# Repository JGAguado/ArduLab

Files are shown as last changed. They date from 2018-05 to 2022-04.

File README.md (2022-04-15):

[][releases]
[](LICENSE)

[][maintenance]
[][buymecoffee]

# ArduLab

The ArduLab board is a robotic platform designed for the ICAI Technological Campus. It has been created with educational purposes for developing robotic proyects based on de [Arduino](https://www.arduino.cc) environment.

<p float="left">
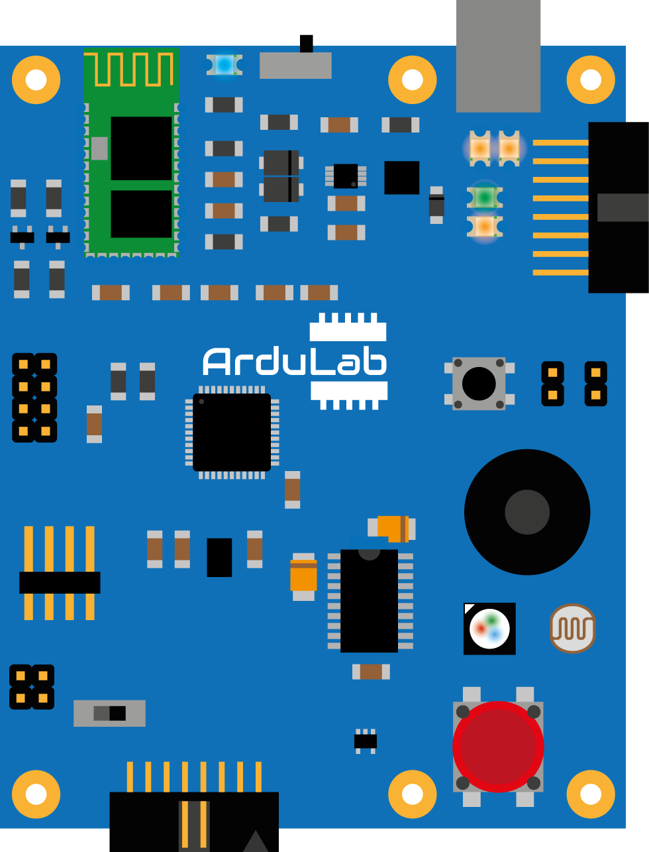
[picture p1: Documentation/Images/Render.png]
   
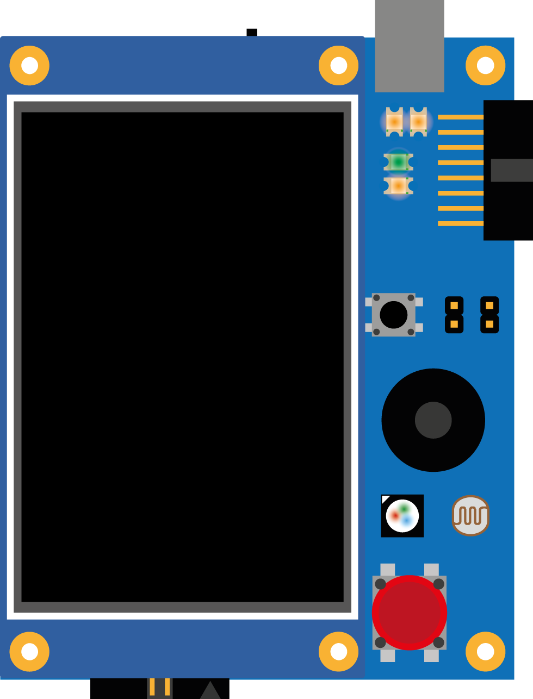
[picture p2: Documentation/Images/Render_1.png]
   
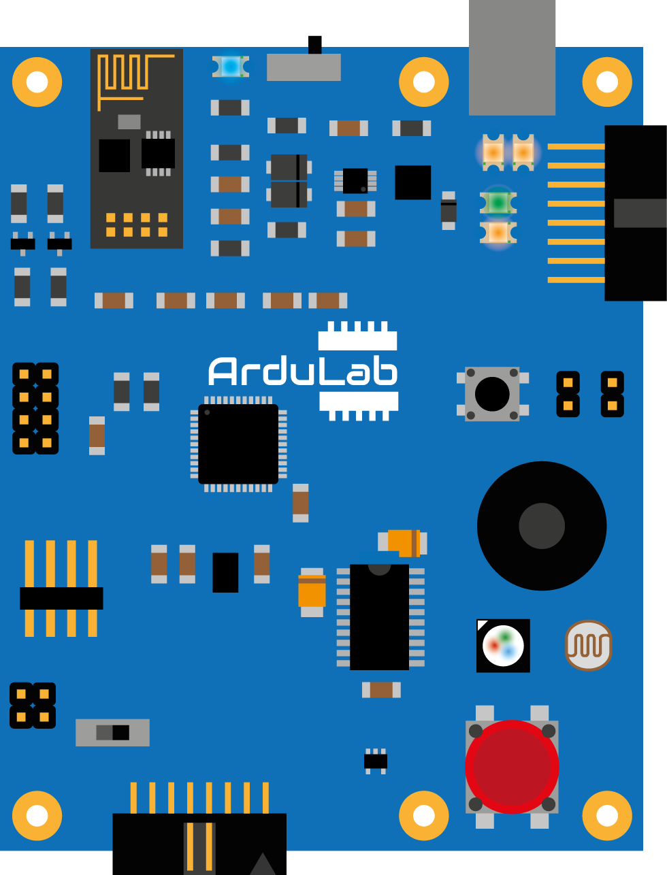
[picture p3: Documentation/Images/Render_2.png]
   
</p>

## Features
* Atmega32U4 microcontroller (same as Arduino Leonardo)
* RGB Led
* LDR
* Buzzer
* Pushbutton
* DC Motor driver (H-Bridge)
* LiPo charging system
* Bluetooth connectivity (HC-05)

It supports the [Itead Nextion Displays](https://www.itead.cc/display/nextion.html) via serial port and also can be plugged directly to the [ElectroLab](https://github.com/SpaceDIY/ElectroLab) board to expand it's functions!

## Project tree

<li><a href="./Hardware/">Hardware</a></li>
<li><a href="./Firmware/">Firmware</a></li>
<li><a href="./Documentation/">Documentation</a></li>

<li><a href="./README.md">README.md</a></li>

[releases-shield]: https://img.shields.io/github/release/JGAguado/ArduLab.svg?style=for-the-badge
[releases]: https://github.com/JGAguado/ArduLab/releases

[license-shield]: https://img.shields.io/badge/License-CC%20BY--NC--SA%204.0-lightgrey.svg?style=for-the-badge

[maintenance-shield]: https://img.shields.io/badge/maintainer-J.%20G.%20Aguado-blue.svg?style=for-the-badge
[maintenance]: https://github.com/JGAguado

[buymecoffee-shield]: https://img.shields.io/badge/buy%20me%20a%20coffee-support-yellow.svg?style=for-the-badge
[buymecoffee]: https://www.buymeacoffee.com/J.G.Aguado

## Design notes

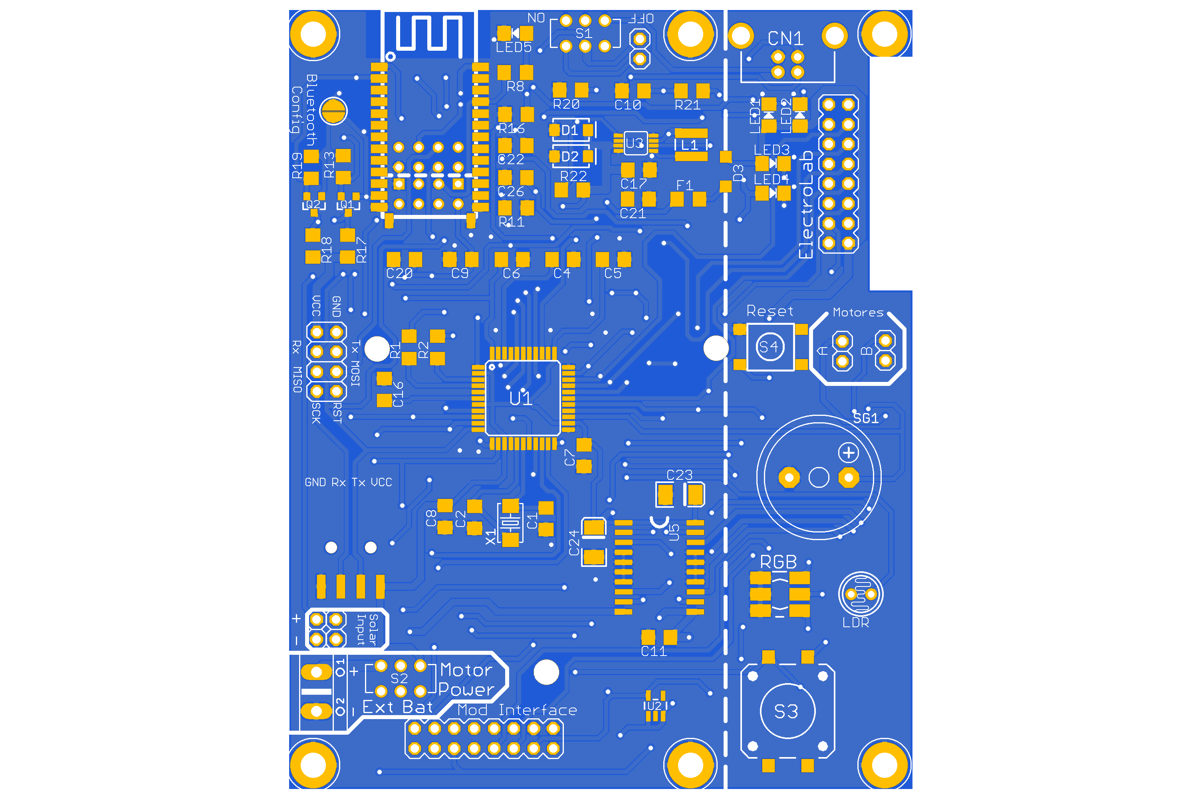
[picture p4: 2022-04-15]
Documentation/Images/Top.png

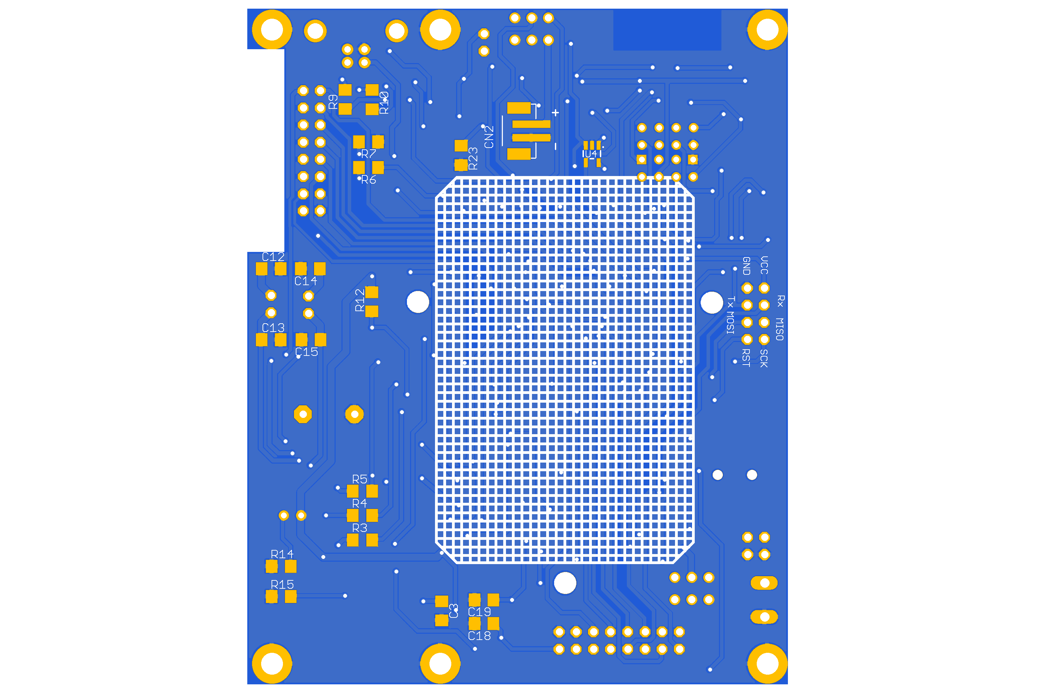
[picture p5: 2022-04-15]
Documentation/Images/Bottom.png

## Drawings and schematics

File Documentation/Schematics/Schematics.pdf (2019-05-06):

A

A

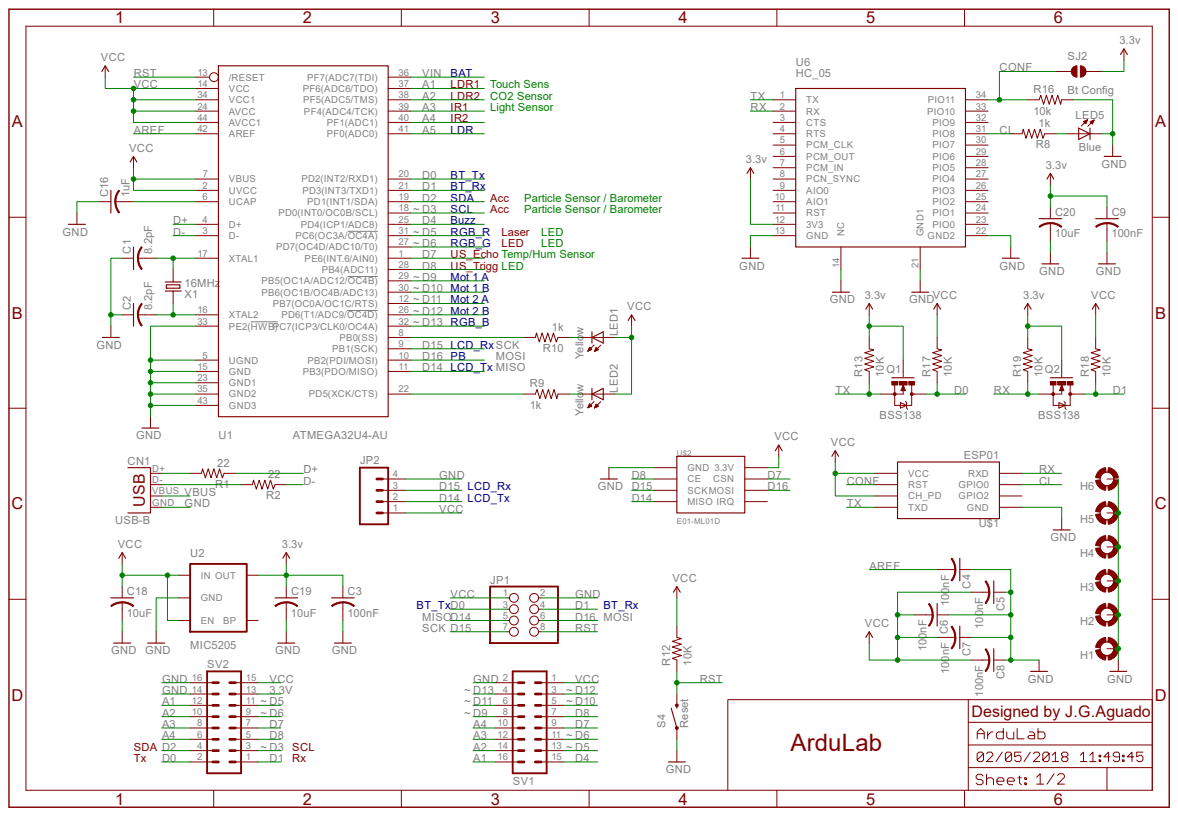
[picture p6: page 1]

A

A

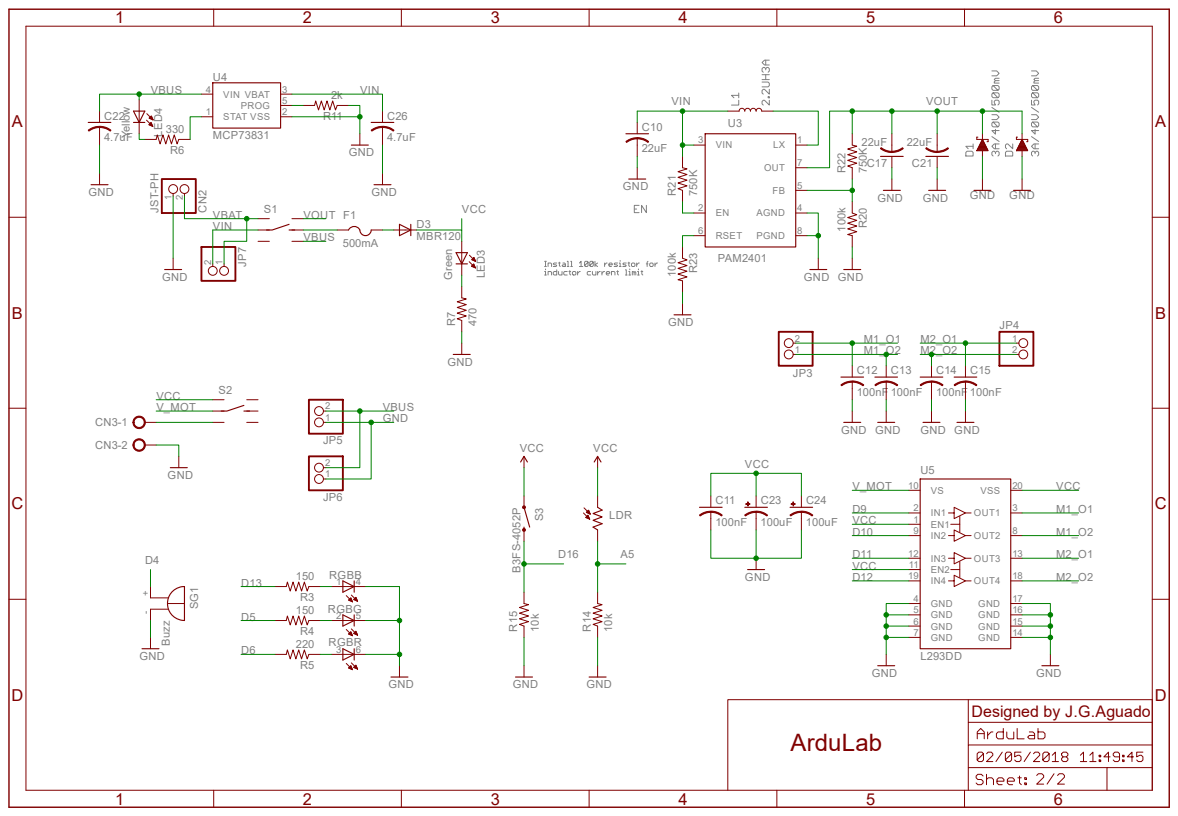
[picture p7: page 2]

GND 14 GND 15 GND 16 GND 17

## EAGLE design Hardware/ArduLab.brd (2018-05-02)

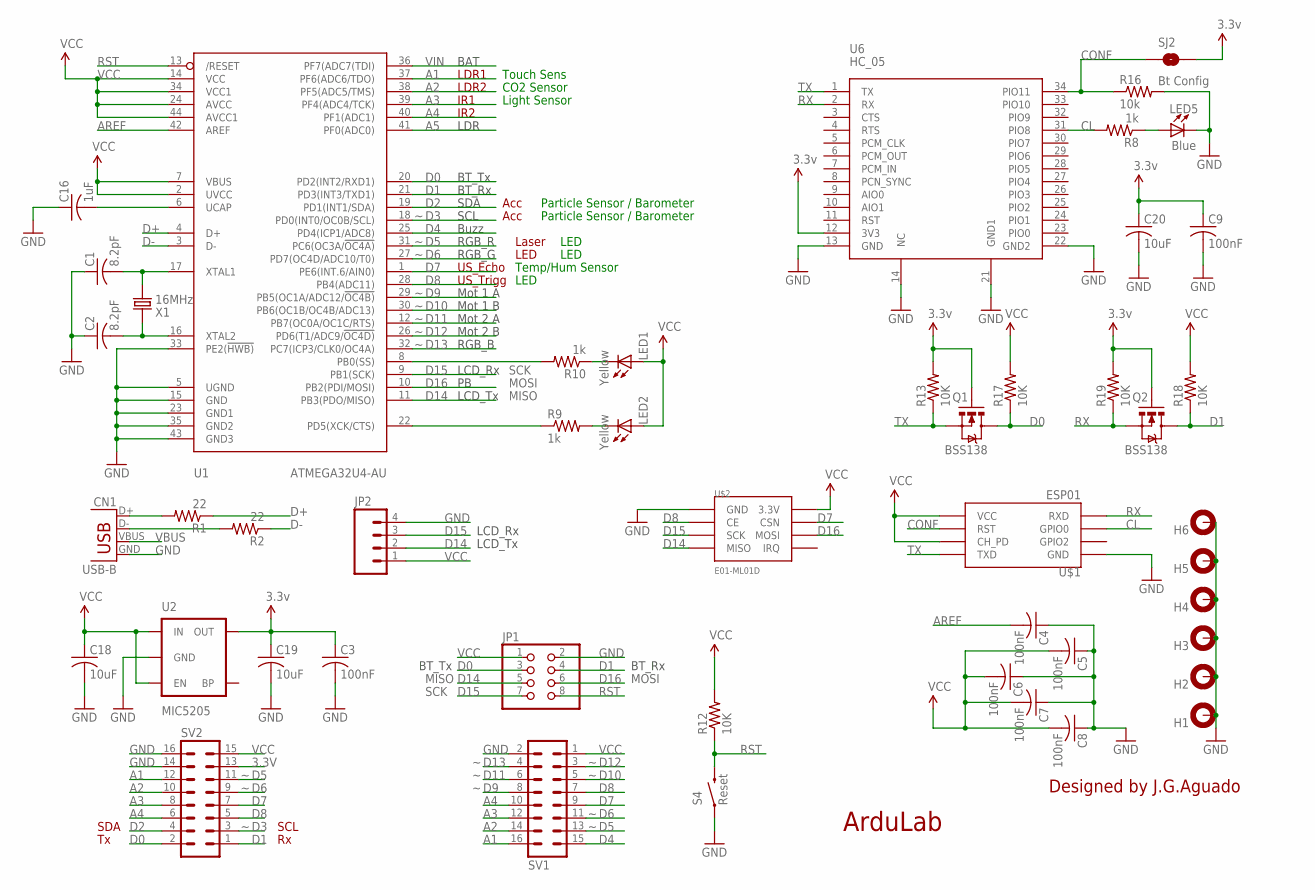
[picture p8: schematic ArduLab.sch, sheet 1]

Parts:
C1, C2: 8.2pF; C1206
C3, C4, C5, C6, C7, C8, C9: 100nF; C1206
C16: 1uF; C1206
C18, C19, C20: 10uF; C1206
CN1: USB-B; USB-B-PTH
H1, H2, H3, H4, H5, H6: MOUNT-PAD-ROUND3.2; 3,2-PAD
JP1: PINHD-2X4; 2X04
JP2: M04SMD; 1X04-SMD
LED1, LED2: Yellow; LED1206
LED5: Blue; LED1206
Q1, Q2: BSS138; SOT23-3
R1, R2: 22; R1206
R8, R9, R10: 1k; R1206
R12, R13, R17, R18, R19: 10K; R1206
R16: 10k; R1206
S4: Reset; TACTILE_SWITCH_TALL
SJ2: Bt Config; SJ_ROUND
SV1, SV2: MA08-2
U1: ATMEGA32U4-AU; TQFP44
U2: MIC5205; SOT23-5
U6: HC_05; BLUETOOTH_SMD
U$1: ESP01
U$2: E01-ML01D
X1: 16MHz; 2P-SMD-5X3.2

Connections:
3.3V: C3.1, C9.1, C19.1, C20.1, Q1.1 (G), Q2.1 (G), R13.2, R19.2, SJ2.2, SV2.13, U2.5 (OUT), U6.12 (3V3), U$1.CH_PD, U$1.VCC, U$2.P$2 (3.3V)
A1: SV1.16, SV2.12, U1.37 (PF6(ADC6/TDO))
A2: SV1.14, SV2.10, U1.38 (PF5(ADC5/TMS))
A3: SV1.12, SV2.8, U1.39 (PF4(ADC4/TCK))
A4: SV1.10, SV2.6, U1.40 (PF1(ADC1))
A5: U1.41 (PF0(ADC0)); also elsewhere on the board
AREF: C4.2, U1.42 (AREF)
CL: R8.2, U6.31 (PIO8), U$1.GPIO0
CONF: R16.1, SJ2.1, U6.34 (PIO11), U$1.RST
D0: JP1.3, Q1.3 (D), R17.1, SV2.2, U1.20 (PD2(INT2/RXD1))
D1: JP1.4, Q2.3 (D), R18.1, SV2.1, U1.21 (PD3(INT3/TXD1))
D2: SV2.4, U1.19 (PD1(INT1/SDA))
D3: SV2.3, U1.18 (PD0(INT0/OC0B/SCL))
D4: SV1.15, U1.25 (PD4(ICP1/ADC8)); also elsewhere on the board
D5: SV1.13, SV2.11, U1.31 (PC6(OC3A/!OC4A)); also elsewhere on the board
D6: SV1.11, SV2.9, U1.27 (PD7(OC4D/ADC10/T0)); also elsewhere on the board
D7: SV1.9, SV2.7, U1.1 (PE6(INT.6/AIN0)), U$2.P$4 (CSN)
D8: SV1.7, SV2.5, U1.28 (PB4(ADC11)), U$2.P$3 (CE)
D9: SV1.8, U1.29 (PB5(OC1A/ADC12/!OC4B)); also elsewhere on the board
D10: SV1.5, U1.30 (PB6(OC1B/OC4B/ADC13)); also elsewhere on the board
D11: SV1.6, U1.12 (PB7(OC0A/OC1C/RTS)); also elsewhere on the board
D12: SV1.3, U1.26 (PD6(T1/ADC9/!OC4D)); also elsewhere on the board
D13: SV1.4, U1.32 (PC7(ICP3/CLK0/OC4A)); also elsewhere on the board
D14: JP1.5, JP2.2, U1.11 (PB3(PDO/MISO)), U$2.P$7 (MISO)
D15: JP1.7, JP2.3, U1.9 (PB1(SCK)), U$2.P$5 (SCK)
D16: JP1.6, U1.10 (PB2(PDI/MOSI)), U$2.P$6 (MOSI); also elsewhere on the board
D17/PB0/RXLED: R10.2, U1.8 (PB0(SS))
D+: R1.1, U1.4 (D+)
D-: R2.1, U1.3 (D-)
GND: C1.1, C2.1, C3.2, C4.1, C5.1, C6.1, C7.1, C8.1, C9.2, C16.1, C18.2, C19.2, C20.2, CN1.GND, H1.B3,2, H2.B3,2, H3.B3,2, H4.B3,2, H5.B3,2, H6.B3,2, JP1.2, JP2.4, LED5.C, R16.2, S4.A2 (1), SV1.2, SV2.14, SV2.16, U1.5 (UGND), U1.15 (GND), U1.23 (GND1), U1.33 (PE2(!HWB)), U1.35 (GND2), U1.43 (GND3), U2.2 (GND), U6.13 (GND), U6.14 (NC), U6.21 (GND1), U6.22 (GND2), U$1.GND, U$2.P$1 (GND); also elsewhere on the board
unnamed: C1.2, U1.17 (XTAL1), X1.2
unnamed: C2.2, U1.16 (XTAL2), X1.1
unnamed: LED2.C, R9.2
unnamed: LED1.C, R10.1
unnamed: CN1.D+, R1.2
unnamed: CN1.D-, R2.2
unnamed: LED5.A, R8.1
PD5/TXLED: R9.1, U1.22 (PD5(XCK/CTS))
RST: JP1.8, R12.1, S4.B2 (2), U1.13 (/RESET)
RX: Q2.2 (S), R19.1, U6.2 (RX), U$1.RX (RXD)
TX: Q1.2 (S), R13.1, U6.1 (TX), U$1.TX (TXD)
UCAP: C16.2, U1.6 (UCAP)
VBUS: CN1.VBUS; also elsewhere on the board
VCC: C5.2, C6.2, C7.2, C8.2, C18.1, JP1.1, JP2.1, LED1.A, LED2.A, R12.2, R17.2, R18.2, SV1.1, SV2.15, U1.2 (UVCC), U1.7 (VBUS), U1.14 (VCC), U1.24 (AVCC), U1.34 (VCC1), U1.44 (AVCC1), U2.1 (IN), U2.3 (EN); also elsewhere on the board
VIN: U1.36 (PF7(ADC7(TDI)); also elsewhere on the board

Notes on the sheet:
ArduLab
Designed by J.G.Aguado
SCK
MOSI
MISO
BAT
BT_Tx
BT_Rx
Acc
Buzz
Mot 1 A
Mot 1 B
Mot 2 B
Mot 2 A
RGB_B
LCD_Tx
LCD_Rx
LDR1
LDR2
IR1
IR2
SDA
SCL
Laser
LED
US_Echo
US_Trigg
Touch Sens
CO2 Sensor
Light Sensor
Particle Sensor / Barometer
Temp/Hum Sensor
RGB_R
RGB_G
LDR

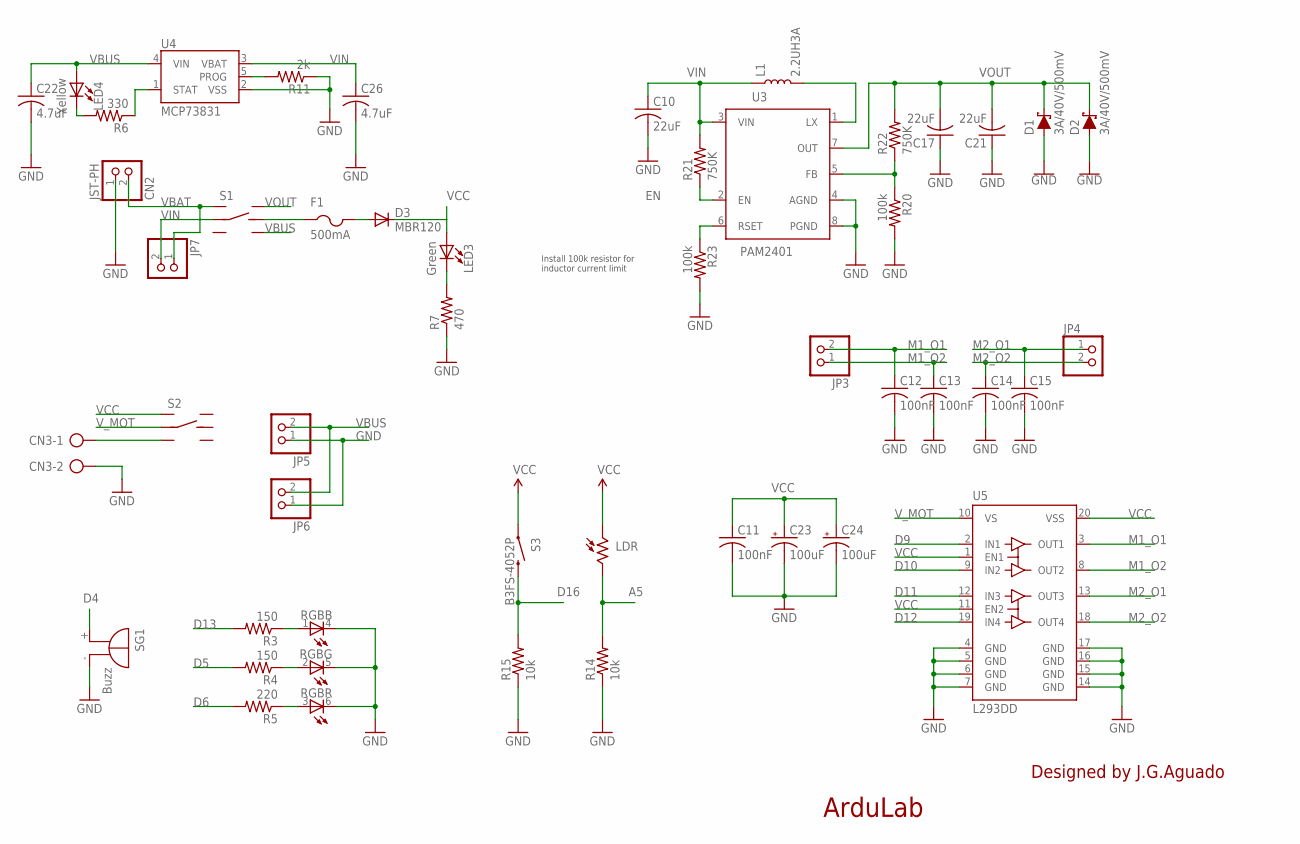
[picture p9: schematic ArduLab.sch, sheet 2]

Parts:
C10, C17, C21: 22uF; C1206
C11, C12, C13, C14, C15: 100nF; C1206
C22, C26: 4.7uF; C3216
C23, C24: 100uF; EIA3528-KIT
CN2: JST-PH; JST-PH-2-SMT
CN3: AK500/2
D1, D2: 3A/40V/500mV; SMA-DIODE
D3: MBR120; SOD123
F1: 500mA; R1206
JP3, JP4, JP5, JP6, JP7: PINHD-1X2; 1X02
L1: 2.2UH3A; INDUCTOR_4X4MM
LDR: VT20N1; TO46-VT200
LED3: Green; LED1206
LED4: Yellow; LED1206
R3, R4: 150; R1206
R5: 220; R1206
R6: 330; R1206
R7: 470; R1206
R11: 2k; R1206
R14, R15: 10k; R1206
R20, R23: 100k; R1206
R21, R22: 750K; R1206
RGB: OVSTRGBBCR8_V2
S1, S2: DPDT_JS202011CQN
S3: B3FS-4052P; TACTILE-SMD-12MM
SG1: Buzz; F/HMB
U3: PAM2401; MSOP8
U4: MCP73831; SOT23-5
U5: L293DD; SO20

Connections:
A5: LDR.2, R14.2; also elsewhere on the board
D4: SG1.+; also elsewhere on the board
D5: R4.2; also elsewhere on the board
D6: R5.2; also elsewhere on the board
D9: U5.2 (IN1); also elsewhere on the board
D10: U5.9 (IN2); also elsewhere on the board
D11: U5.12 (IN3); also elsewhere on the board
D12: U5.19 (IN4); also elsewhere on the board
D13: R3.2; also elsewhere on the board
D16: R15.2, S3.3 (2); also elsewhere on the board
EN: R21.1, U3.2 (EN)
GND: C10.2, C11.2, C12.2, C13.2, C14.2, C15.2, C17.1, C21.1, C22.2, C23.C (-), C24.C (-), C26.2, CN2.1 (2), CN3.2, D1.A, D2.A, JP5.1, JP6.1, R7.1, R11.1, R14.1, R15.1, R20.2, R23.2, RGB.4 (C), RGB.5 (C), RGB.6 (C), SG1.-, U3.4 (AGND), U3.8 (PGND), U4.2 (VSS), U5.4 (GND), U5.5 (GND), U5.6 (GND), U5.7 (GND), U5.14 (GND), U5.15 (GND), U5.16 (GND), U5.17 (GND); also elsewhere on the board
M1_O1: C12.1, JP3.2, U5.3 (OUT1)
M1_O2: C13.1, JP3.1, U5.8 (OUT2)
M2_O1: C15.1, JP4.1, U5.13 (OUT3)
M2_O2: C14.1, JP4.2, U5.18 (OUT4)
unnamed: R20.1, R22.1, U3.5 (FB)
unnamed: F1.1, S1.5 (RC)
unnamed: L1.P$2 (2), U3.1 (LX)
unnamed: R23.1, U3.6 (RSET)
unnamed: LED4.C, R6.2
unnamed: R11.2, U4.5 (PROG)
unnamed: R6.1, U4.1 (STAT)
unnamed: LED3.C, R7.2
unnamed: D3.A, F1.2
unnamed: R3.1, RGB.1 (A)
unnamed: R4.1, RGB.2 (A)
unnamed: R5.1, RGB.3 (A)
VBAT: CN2.2 (1), JP7.1, S1.1 (L1)
VBUS: C22.1, JP5.2, JP6.2, LED4.A, S1.6 (R2), U4.4 (VIN); also elsewhere on the board
VCC: C11.1, C23.A (+), C24.A (+), D3.C, LDR.1, LED3.A, S2.1 (L1), S3.1, U5.1 (EN1), U5.11 (EN2), U5.20 (VSS); also elsewhere on the board
VIN: C10.1, C26.1, JP7.2, L1.P$1 (1), R21.2, S1.2 (LC), U3.3 (VIN), U4.3 (VBAT); also elsewhere on the board
VOUT: C17.2, C21.2, D1.C, D2.C, R22.2, S1.4 (R1), U3.7 (OUT)
V_AUX: CN3.1, S2.3 (L2)
V_MOT: S2.2 (LC), U5.10 (VS)

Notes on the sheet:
ArduLab
Designed by J.G.Aguado
Install 100k resistor for inductor current limit

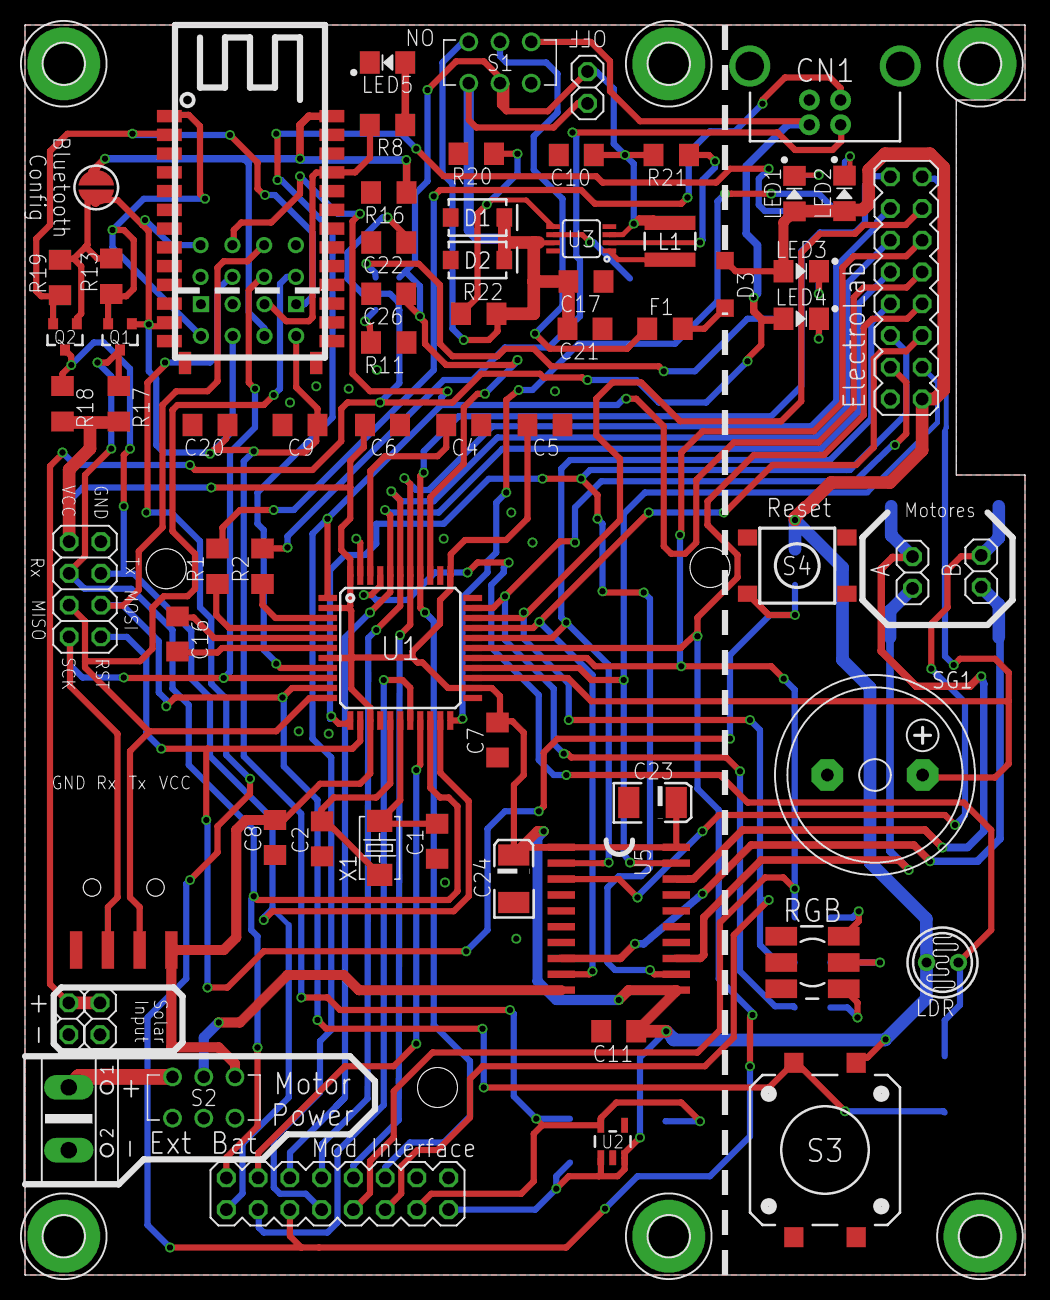
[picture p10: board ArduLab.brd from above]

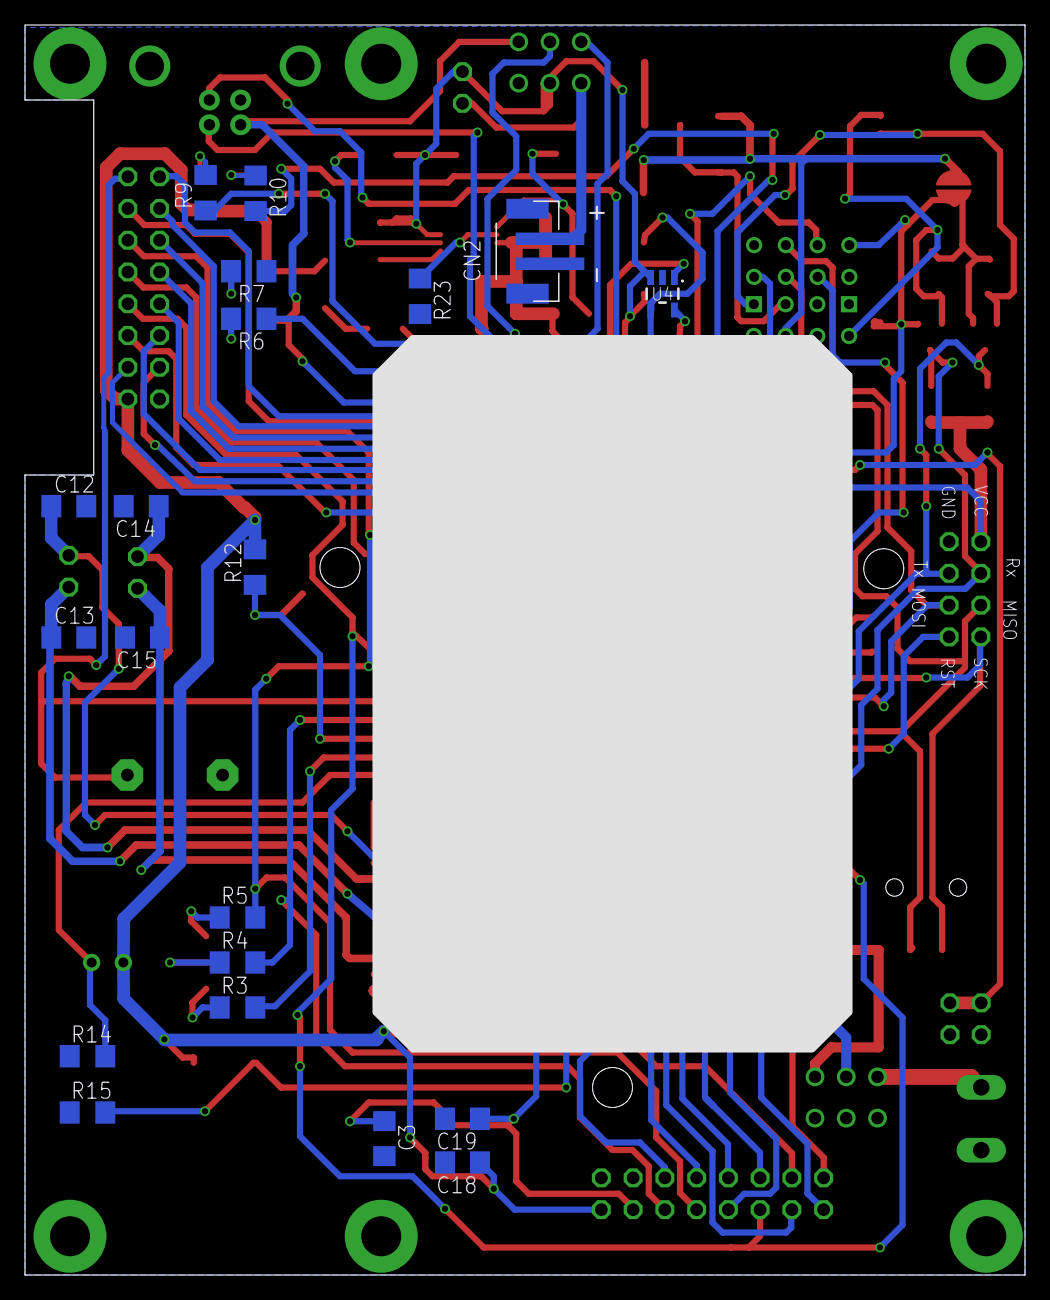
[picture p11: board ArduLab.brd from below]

Board: 2 copper layers, 80.0 x 100.0 mm, 95 parts (20 on the bottom side), 66 nets.

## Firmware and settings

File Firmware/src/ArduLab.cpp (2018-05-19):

/******************************************************************************

ArduLab.cpp
Library for managing ArduLab board.
Created by J.G.Aguado
May 18, 2018  
https://github.com/SpaceDIY/ArduLab

This code is released under the [MIT License](http://opensource.org/licenses/MIT).
Please review the LICENSE.md file included with this example. If you have any questions 
or concerns with licensing, please contact techsupport@sparkfun.com.
Distributed as-is; no warranty is given.

******************************************************************************/
 
#include "ArduLab.h"

ArduLab::ArduLab(char Mod, char Comms)
{
  // Basic Outputs
  pinMode(_buzzer, OUTPUT);
  pinMode(_red, OUTPUT);
  pinMode(_green, OUTPUT);
  pinMode(_blue, OUTPUT);

  // H-Bridge for motor
  pinMode(_motor_a_1, OUTPUT);
  pinMode(_motor_a_2, OUTPUT);
  pinMode(_motor_b_1, OUTPUT);
  pinMode(_motor_b_2, OUTPUT);

  // Basic Inputs
  pinMode(_pushbutton, INPUT);

  if (Mod == "ElectroLab"){
    _mod = 1;
  }
  else if (Mod == "BotMod"){
    _mod = 2;
  }
  else if (Mod == "DomoMod"){
    _mod = 3;
  }
  else if (Mod == "KineticMod"){
    _mod = 4;
  }

  if (Comms == "Wifi"){
    _comms = 1;
  }
  else if (Comms == "Bluetooth"){
    _comms = 2;
  }
  else if (Mod == "RF24"){
    _comms = 3;
  }
}
 
void ArduLab::Beep()
{
  digitalWrite(_buzzer, HIGH);
  delay(250);
  digitalWrite(_buzzer, LOW);
  delay(250);  
}

void ArduLab::RGB(int r, int g, int b)
{
	analogWrite(_red, r);
	analogWrite(_green, g);
	analogWrite(_blue, b);
}

boolean ArduLab::PushButton()
{
  return digitalRead(_pushbutton);
}

float ArduLab::Battery()
{
  return analogRead(_battery);
}

float ArduLab::Light()
{
  return analogRead(_ldr);
}

void ArduLab::MotorA(int dir)
{
  if (dir == 0){
    digitalWrite(_motor_a_1, LOW);
    digitalWrite(_motor_a_2, LOW);    
  }
  else if (dir == 1){
    digitalWrite(_motor_a_1, HIGH);
    digitalWrite(_motor_a_2, LOW);    
  }
  else if (dir == 2){
    digitalWrite(_motor_a_1, LOW);
    digitalWrite(_motor_a_2, HIGH);    
  }
}

void ArduLab::MotorB(int dir)
{
  if (dir == 0){
    digitalWrite(_motor_b_1, LOW);
    digitalWrite(_motor_b_2, LOW);    
  }
  else if (dir == 1){
    digitalWrite(_motor_b_1, HIGH);
    digitalWrite(_motor_b_2, LOW);    
  }
  else if (dir == 2){
    digitalWrite(_motor_b_1, LOW);
    digitalWrite(_motor_b_2, HIGH);    
  }
}

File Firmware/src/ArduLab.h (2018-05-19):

/******************************************************************************

ArduLab.h
Library for managing ArduLab board.
Created by J.G.Aguado
May 18, 2018  
https://github.com/SpaceDIY/ArduLab

This code is released under the [MIT License](http://opensource.org/licenses/MIT).
Please review the LICENSE.md file included with this example. If you have any questions 
or concerns with licensing, please contact techsupport@sparkfun.com.
Distributed as-is; no warranty is given.

******************************************************************************/

#ifndef ArduLab_h
#define ArduLab_h
 
#if (ARDUINO >= 100)
#include "Arduino.h"
#else
#include "WProgram.h"
#endif

class ArduLab{
    public:
        ArduLab(char Mod, char Comms);
        void RGB(int r, int g, int b);
        void Beep();
        bool PushButton();
        float Battery();
        float Light();
        void MotorA(int dir);
        void MotorB(int dir);
    private:
    	int _mod = 0;
    	int _comms = 0;
    	
    	int _buzzer = 4;
    	int _red = 13;
    	int _green = 5;
    	int _blue = 6;
    	int _pushbutton = 16;
    	int _battery = A0;
    	int _ldr = A5;

    	int _motor_b_1 = 9;
    	int _motor_b_2 = 10;
    	int _motor_a_1 = 11;
    	int _motor_a_2 = 12;
};
#endif

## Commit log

2017-12-26 Initial commit V1
    First prototype board
    [ArduLab.brd, ArduLab.sch]
2017-12-26 Fixed bug: Battery connector polarity
    [ArduLab.brd, ArduLab.sch]
2017-12-26 Modified: Center pad of U3 (TPS61030) wired to ground
    [ArduLab.brd, ArduLab.sch]
2017-12-27 Bluetooth-microcontroller communication improved with shift level conversor.
    [ArduLab.brd, ArduLab.sch]
2017-12-27 Added support for ESP8266-01
    [ArduLab.brd, ArduLab.sch]
2017-12-28 LiPo power boosting circuit based in PAM2401 IC
    [ArduLab.brd, ArduLab.sch]
2017-12-29 Added support for Serial interface in Mod connector
    [ArduLab.brd, ArduLab.sch]
2017-12-29 Updated Mod Interface for RadioLab compatibility
    [ArduLab.brd, ArduLab.sch]
2017-12-29 New Mod Interface position layout (25x6.5mm)
    [ArduLab.brd]
2018-01-14 SCH and BRD updated. Added Production files (GERBER, BOM and CENTROID)
    [ArduLab.GBL, ArduLab.GBO, ArduLab.GBP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]
2018-01-17 Update gerber for production
    [BOM ArduLab.csv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]
2018-02-01 Added drill hole for battery holding.
    [ArduLab.brd]
2018-02-03 Minor SCH Updates: V1.0 label removed
    [ArduLab.sch]
2018-02-03 Minor BRD updates and Production files regenerated: -Layout correction.
    [ArduLab.brd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]
2018-02-03 Schematics PDF uploaded
2018-02-03 Centroid update
    [ArduLab_centroid.csv]
2018-02-09 Added R23 (100k) as optional resistor for inductor current limit
    [ArduLab.brd, ArduLab.sch, ArduLab_centroid.csv]
2018-02-22 Updated Production files
    [ArduLab.GBL, ArduLab.GBO, ArduLab.GBP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]
2018-04-28 Added PTC reset fuse 6V 500mA. Package 1206. Part number: 1206L050YR
    [ArduLab.brd, ArduLab.sch]
2018-04-28 Connection between pin A0 and battery voltage pin for monitoring the battery status.
    [ArduLab.brd, ArduLab.sch]
2018-04-28 2.4GHz RF ML01D Module Integration
    [ArduLab.brd, ArduLab.sch]
2018-05-02 Updated components silkscreen layout
    [ArduLab.brd, ArduLab.sch]
2018-05-19 Added Schematics.pdf
2022-04-15 Updated structure
    [ArduLab.GBL, ArduLab.GBO, ArduLab.GBP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]

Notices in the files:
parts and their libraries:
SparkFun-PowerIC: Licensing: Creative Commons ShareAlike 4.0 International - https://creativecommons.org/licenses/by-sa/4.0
